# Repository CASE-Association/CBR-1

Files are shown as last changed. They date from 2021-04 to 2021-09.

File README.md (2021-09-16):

# CBR-1
Case Balancing Robot 1

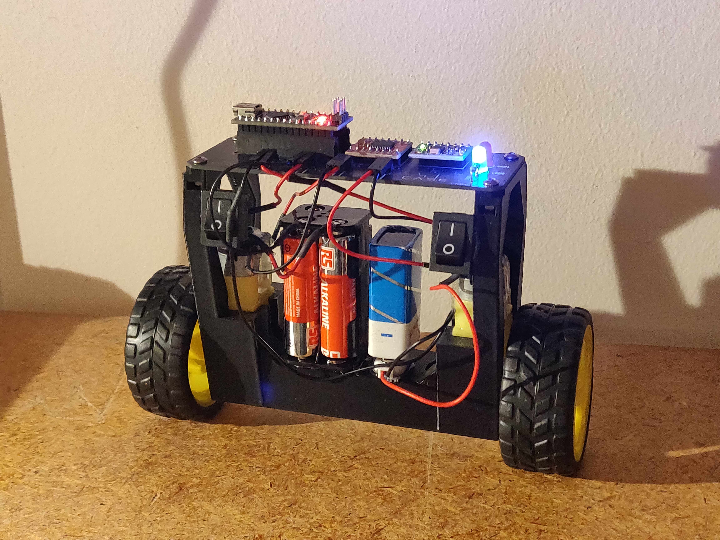
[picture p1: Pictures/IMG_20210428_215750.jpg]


Beginner balancing robot developed by CASE Association.

# Bill of materials
  - 1 x Arduino Nano
  - 1 x TB6612FNG (DC motor driver)
  - 1 x MPU6050 (Inertial measurement unit)
  - 1 x CBR-1 3D-printed chassi
  - 2 x 6V DC motors (with wheels)
  - 1 x Rockerswitch or other switch (between 9V battery and PCB)
  - 1 x 4xAA batteryholder
  - 1 x 9V batteryholder
  - 4 x M3x10 screw (M3x12 might also work)
  - 4 x M3 nut
  - Wires
  - Heatshrink
  - 4 x AA batteries (there are some in the lab you can try out with your bot with but it's a good idea to bring your own batteries)
  - 1 x 9V battery (same with AA batteries, it's nice to bring your own)

Optional:

  - 1 x Rockerswitch or other switch (now between the 4xAA batteryholder and PCB)
  - 2 x LED
  - 2 x Resistors R1 and R2
  - Various pin-connectors
For R1 and R2, use whatever resistance you prefer for LEDs in these applications, but around 300 ohm works fine. We used 100 Ohm for a red LED and 300 Ohm for a blue LED.

All of the components are available to purchase in the iZettle, but feel free to use your own components if you for instance want a more powerful battery to power the motors. The most important thing is that you are able to supply 9-12 V to the Arduino and at least 6 V to the motors (a somewhat higher voltage will work, you'll get more power!). Using 4xAA (4 in series) is the absolute minimum battery solution, considering the max current you get from them.

The 3D-printed chassi can, if not bought through iZettle, be redesigned and 3D-printed if you like. The STL file is provided in the CAD folder, and you can also design things to add to the robot! The picture below shows an example of a way to increase the distance between the ground and the centrum of mass by placing the batteries on top. This makes it easier for the robot to balance!

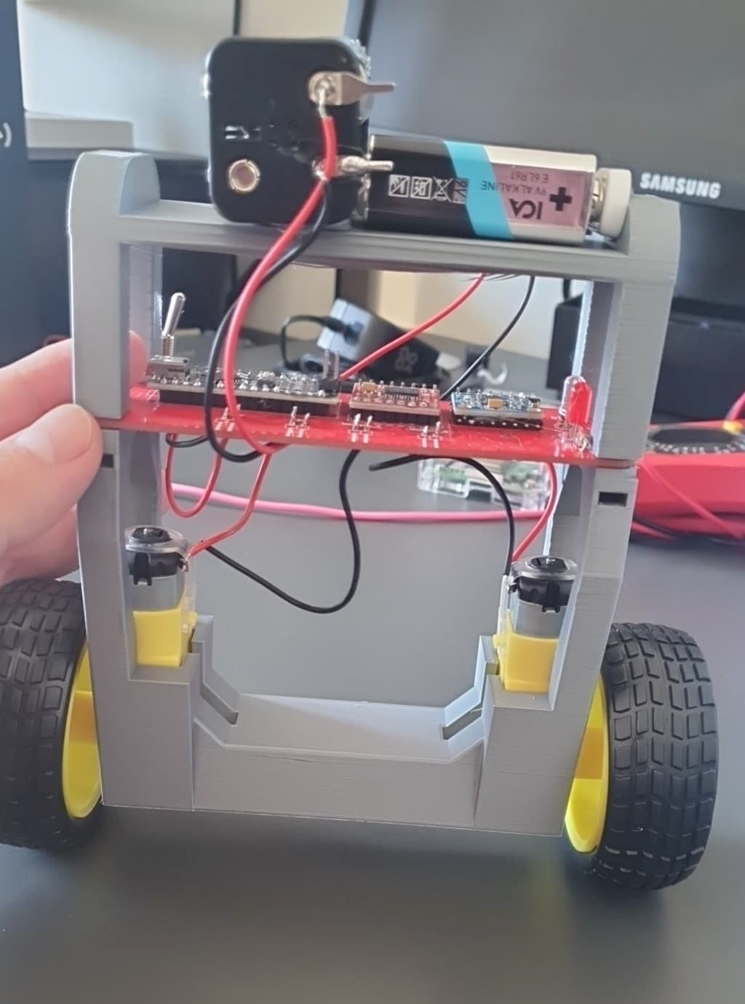
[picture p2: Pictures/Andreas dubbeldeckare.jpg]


The STL file for this extra piece can also be found in the CAD folder.

# Soldering
There's quite a bit of it.

## Soldering components to the PCB

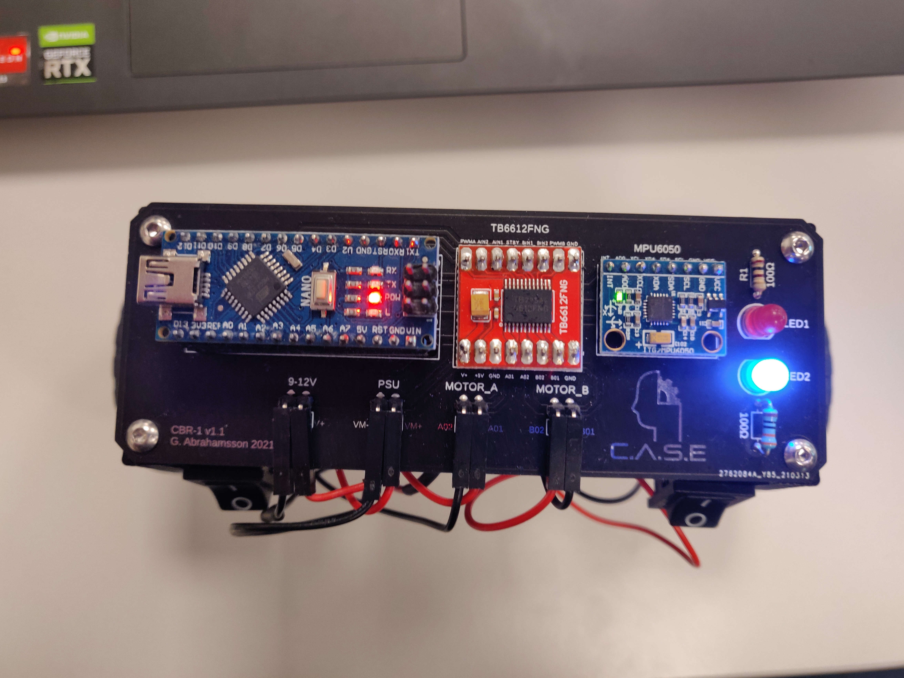
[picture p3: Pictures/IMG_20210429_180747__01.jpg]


The three main components to solder to the PCB are:

  - Arduino Nano
  - TB6612FNG
  - MPU6050

The PCB is marked where to attach each component, but you can solder in two ways:

### Directly to the PCB
This gives the most clean look, but can be quite troublesome if something goes wrong. It's very important that you orient the components in the correct way (they fit both ways, but only one works)! Double check that the ports on the components match the ones on the PCB before soldering.

### With female pin connectors to the PCB
Solder female pin connectors to the PCB and then attach your components to them. This way you can reuse components if you don't feel like buying the same component for another project in the future. If a component fails, you can also replace them much easier.

## LEDs
If you want LEDs on your robot, solder them to the PCB with their respective resistor. Don't forget that LEDs are Light Emitting *Diodes*.The kathode (the shorter pin) must be put into the hole near the "flat side" of the footprint on the PCB. The anode (the longer pin) must be put into the hole near the "round side".

## Wiring

Don't forget heatshrink before you solder!

Connectors can be soldered to the ports for 6-12 V, powersupply (marked "PSU" or "6V"), motor A and motor B if you like. This makes it easier to detach parts of the robot without needing to desolder anything. In the example on page 1, 90° male pin connectors are used on the PCB while the motors and batteries all have female pin connectors soldered to their respective cables.

### Batterypacks
If you only want to use one switch, use it with the 9V battery. This ensures that the only switch used is turning the Arduino Nano on/off (since the 9-12V port is powering the Nano and PSU/6V is powering the motors).
The switch can be between the battery and the positive or the negative pin on the PSU/6V ports, since it's breaking the circuit. We soldered the already attached red wire from the 9V battery to one pin on the switch, and then another wire (dupont-cable with one end cut off) on the other pin on the switch. Another dupont cable was soldered to the other wire from the battery holder to make sure it has a female connector.

The same was done with the 4xAA battery holder, but the wires were soldered to the pins since this particular battery holder does not come with wires already attached.

Repeat this for the other pack, but ignore the switch if you do not want to use two of them. Remember, having control over both batterypacks while the robot is in action is very helpful. We recommend two switches!

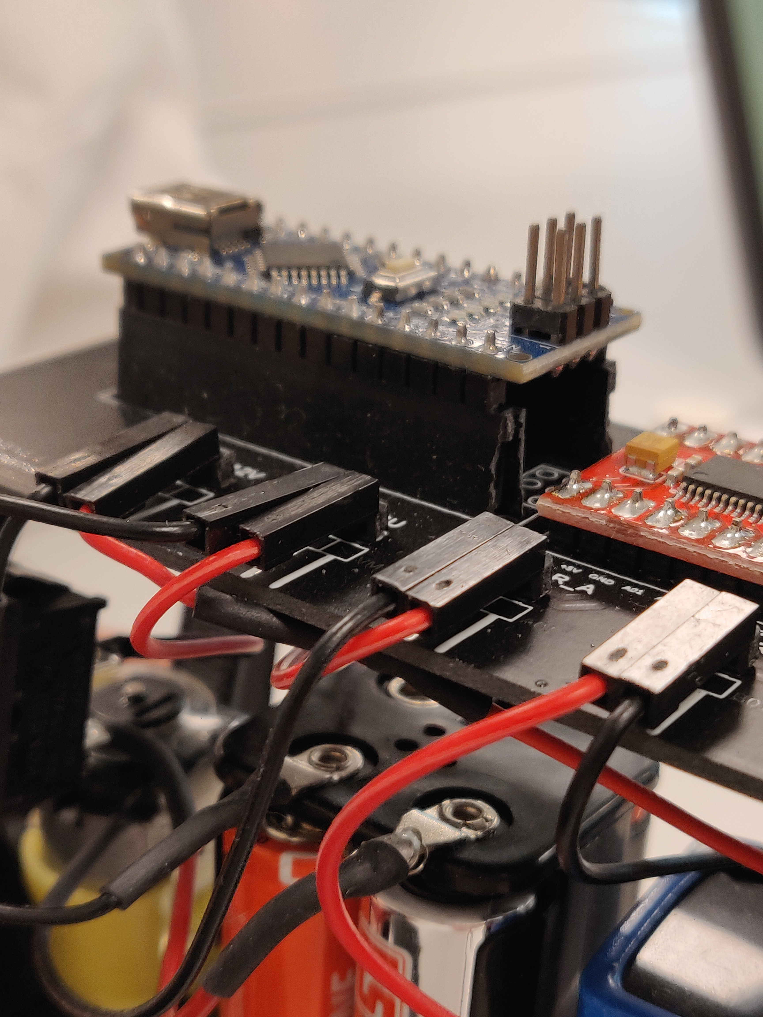
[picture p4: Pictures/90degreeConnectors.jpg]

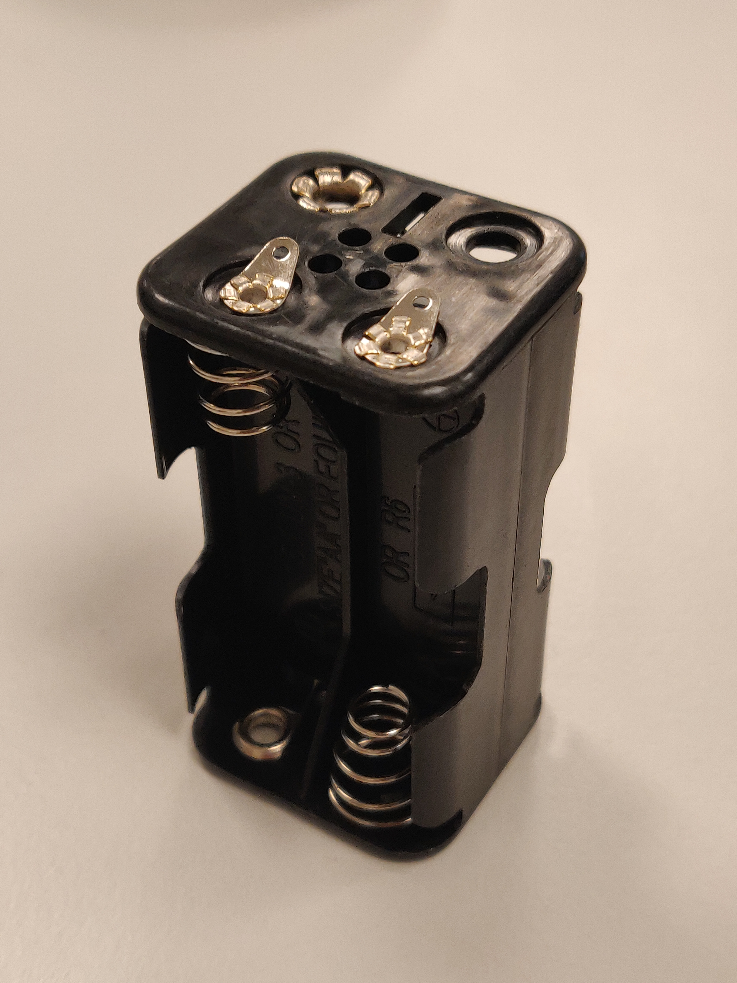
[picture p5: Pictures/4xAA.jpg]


When soldering wires to the batterypacks, don't forget to use red for positive and black for negative! Things get very problematic if they are mixed up!

### Motors
For each motor, solder wires to each of the connections on the motor. Heatshrink is good to use here (don't for get to put it on before you solder!), and applying some hot glue around the connection after everything is done will decrease the risk of the copper breaking from bending. Also, using dupont cables with female pin connectors is a fast way to get wires without having to attach connectors to the end of the wires. Just cut one end off and keep the other!

If the wheels aren't already attached, attach them now.

# Assembly
Bring out the glue gun! 

## Gluing

Everything except for the PCB is attached with hot glue, so just glue on the motors and batterypacks! Remember not to orient the packs in a way where you can't remove/attach batteries.

## PCB
Drop in an M3 nut in each hole and screw on the PCB with the M3 screws. It's possible to glue the PCB to the chassi but it's made to be assembled with nuts and screws. 

## Connecting the wires
If you're not using connectors, replace "connect" with "solder":
  - Connect the wires from the 9V battery holder to the 9-12V port.
  - Connect the wires from the 4xAA battery holder to the PSU/6V port.
  - Connect the wires from one of the motor to the "Motor A" port. It does not matter which wire goes to which pin, this can be corrected in the code if the motor turns the wrong way.
  - Connect the wires from the other motor to the "Motor B" port.

The robot is now fully assembled!

# Software

PlatformIO was used for this project. The code can be found in the "Code" folder.

## Libraries
The following libraries are needed:
  - PID_v1.h
  - I2Cdev.h
  - MPU6050_6Axis_MotionApps20.h

Make sure they are in your project!

## Using the code

Upload the code to the Nano. Do not freak out if it doesn't work at first! There's a few things that might need to be adjusted.

### Motor rotation directions
When tilting the robot to one direction, the motors should turn in a way that drives it in that direction. If a specific motor does not turn that direction, you can switch the connectors.
This will switch the direction the motor turns. Do this to both motors so that they drive in the direction the robot tilts.

If you do not have connectors, but have soldered the wires to each port, you can switch the direction of the motors in the code.
This is done by changing the LOW to HIGH or HIGH to LOW of both ports on a specific motor in the functions *Forward* and *Reverse*.
Having in1A LOW and in2A HIGH will rotate the motor in one direction, and switching in1A to HIGH and in2A to LOW will make it rotate
the other direction.

top

You can achieve the same effect by switching the output from negative to positive or vice versa:

top

### Calibration
The robot might not perform optimally with the default values included. This will be fixed here.

#### Target angle
If the robot is trying to escape everytime you set it down, you might have to calibrate the setpoint.
If it's too low or too high, the robot will correct itself to a too low of an angle, making it tilt and therefore accelerating
in that direction.

top

Problems with the setpoint can also occur if the MPU6050 is not soldered/connected parallell to the PCB.
If you feel comfortable trying to bend it parallell, go ahead, but adjusting the setpoint in the code also works.

#### PID
If the robot isn't balancing, or trying too violently, you can adjust the PID values (especially if you've attached the batteries
in another way compared to ours at the top of this page!).

Start by adjusting the *Kp* value. This affects the output based on the difference from the measured and target value.
If it's too slow or "weak", increase the value. If it's too violent and jerky, decrease the value.

After that, move on to *Kd*. This affects the output based on the derivative.
If it's too jittery, reduce the value.

Lastly, adjust *Ki*. This affects the output based on the integral.
Start from a low value and increase it until it works.

It should now balance on its own!

#### LEDs
You can control the LEDs (if you have them) by writing a 1 or a 0 to their respective ports:

top

In the provided code, the LEDs will show which direction the robot is currently travelling in.

# Improvements

There's a lot about this robot that can be improved. Here's a list of things to improve if you'd like:
  - 3D-printed chassi: Design your own chassi or some piece to be attached to it! The center of mass needs to get higher!
  - Code that takes velocity into concideration: Currently, the robot is satisfied as long as it's standing upright, even if its travelling at max speed. Try to fix this in the code!
  - Improved PCB: If you're into SMD, you can design a PCB with no throughhole components and only surface mounted ones. It will look much cooler!
  - Wireless controls: You could attach for instance an NRF24L01 to enable wireless communication with a controller!
  - Other batteries: It is possible to use for instance LiPo batteries to enable more power, while also only needing one battery.
  - Measure the angle that the motors rotate to: Since regular DC motors and no stepper motors (or something similar) are used in this project, the robot does not know how much the wheels have actually rotated. It is possible to use sensors to measure this and to use the information in conjunction with the controls-code.

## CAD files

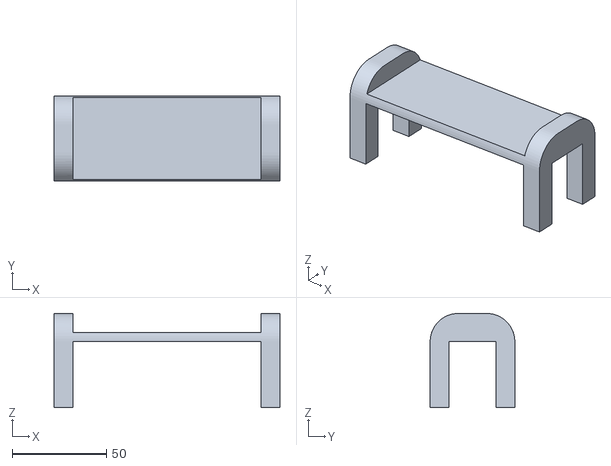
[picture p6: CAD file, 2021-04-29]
CAD/Brygga-Balans-v1.stl
120.0 x 45.0 x 50.0

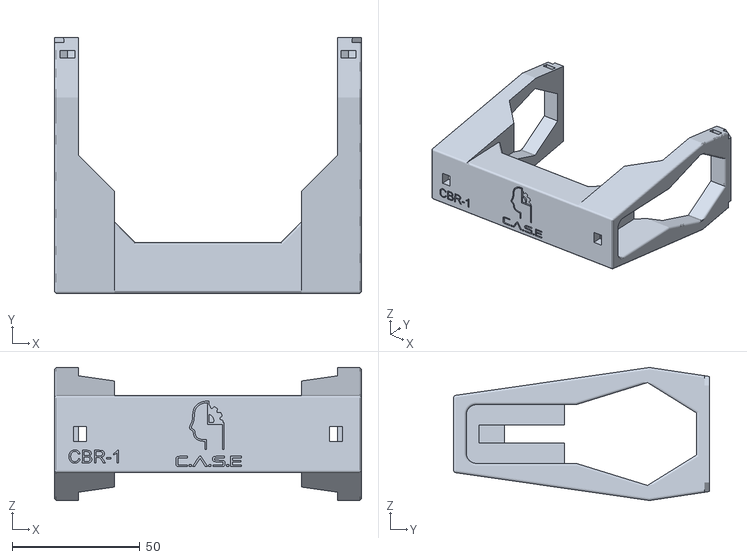
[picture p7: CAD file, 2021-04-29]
CAD/CBR-1 Chassi 2.2.stl
120.0 x 100.0 x 52.0

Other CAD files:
PCB/CBR-1_PCB_Design v36.f3z

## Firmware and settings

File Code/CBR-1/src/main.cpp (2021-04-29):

#include <Arduino.h>
#include <PID_v1.h>
#include <I2Cdev.h>
#include <MPU6050_6Axis_MotionApps20.h>
 
int pwmA = 5;
int in1A = 3;
int in2A = 4;
 
int pwmB = 6;
int in1B = 7;
int in2B = 8;

int LED2 = 11;
int LED1 = 12;
 
int n1 = 0;
int n2 = 0;

MPU6050 mpu;

// MPU control/status vars
bool dmpReady = false;  // set true if DMP init was successful
uint8_t mpuIntStatus;   // holds actual interrupt status byte from MPU
uint8_t devStatus;      // return status after each device operation (0 = success, !0 = error)
uint16_t packetSize;    // expected DMP packet size (default is 42 bytes)
uint16_t fifoCount;     // count of all bytes currently in FIFO
uint8_t fifoBuffer[64]; // FIFO storage buffer

// orientation/motion vars
Quaternion q;           // [w, x, y, z]         quaternion container
VectorFloat gravity;    // [x, y, z]            gravity vector
float ypr[3];           // [yaw, pitch, roll]   yaw/pitch/roll container and gravity vector

/*********Tune these 4 values for your BOT*********/

double setpoint = 180; //set the value when the bot is perpendicular to ground using serial monitor. 

//#############################################
//Change those Values according to your Design
//#############################################
double Kp = 15;  // Set this first
double Ki = 200; // Finally set this 
double Kd = 0.6; // Set this second
//#############################################

double input, output;
PID pid(&input, &output, &setpoint, Kp, Ki, Kd, DIRECT);

volatile bool mpuInterrupt = false;     // indicates whether MPU interrupt pin has gone high

void dmpDataReady()
{
    mpuInterrupt = true;
}


void Forward() //Code to rotate the wheel forward 
{
    digitalWrite(LED1,0);
    digitalWrite(LED2,1);
    
    digitalWrite(in1A, HIGH);
    digitalWrite(in2A, LOW);
 
    digitalWrite(in1B, HIGH);
    digitalWrite(in2B, LOW);

    analogWrite(pwmA, output);
    analogWrite(pwmB, output);

    Serial.print("F"); //Debugging information 
}

void Reverse() //Code to rotate the wheel Backward  
{
    digitalWrite(LED1,1);
    digitalWrite(LED2,0);

    digitalWrite(in1A, LOW);
    digitalWrite(in2A, HIGH);
 
    digitalWrite(in1B, LOW);
    digitalWrite(in2B, HIGH);

    analogWrite(pwmA, -1*output);
    analogWrite(pwmB, -1*output);

    Serial.print("R");
}

void Stop() //Code to stop both the wheels
{
    digitalWrite(LED1,0);
    digitalWrite(LED2,0);

    digitalWrite(in1A, LOW);
    digitalWrite(in2A, LOW);
 
    digitalWrite(in1B, LOW);
    digitalWrite(in2B, LOW);

    analogWrite(pwmA, 0);
    analogWrite(pwmB, 0);

    Serial.print("S");
}

void setup(){

  pinMode(pwmA, OUTPUT);
  pinMode(pwmB, OUTPUT);
  pinMode(in1A, OUTPUT);
  pinMode(in2A, OUTPUT);
  pinMode(in1B, OUTPUT);
  pinMode(in2B, OUTPUT);

  pinMode(LED1,OUTPUT);
  pinMode(LED2,OUTPUT);


  //Serial.begin(9600);
  
  // initialize device
    Serial.println(F("Initializing I2C devices..."));
    mpu.initialize();

     // verify connection
    Serial.println(F("Testing device connections..."));
    Serial.println(mpu.testConnection() ? F("MPU6050 connection successful") : F("MPU6050 connection failed"));

    // load and configure the DMP
    devStatus = mpu.dmpInitialize();

    
    // supply your own gyro offsets here, scaled for min sensitivity
    mpu.setXGyroOffset(220);
    mpu.setYGyroOffset(76);
    mpu.setZGyroOffset(-85);
    mpu.setZAccelOffset(1688); 

      // make sure it worked (returns 0 if so)
    if (devStatus == 0)
    {
        // turn on the DMP, now that it's ready
        Serial.println(F("Enabling DMP..."));
        mpu.setDMPEnabled(true);

        // enable Arduino interrupt detection
        Serial.println(F("Enabling interrupt detection (Arduino external interrupt 0)..."));
        attachInterrupt(0, dmpDataReady, RISING);
        mpuIntStatus = mpu.getIntStatus();

        // set our DMP Ready flag so the main loop() function knows it's okay to use it
        Serial.println(F("DMP ready! Waiting for first interrupt..."));
        dmpReady = true;

        // get expected DMP packet size for later comparison
        packetSize = mpu.dmpGetFIFOPacketSize();
        
        //setup PID
        pid.SetMode(AUTOMATIC);
        pid.SetSampleTime(10);
        pid.SetOutputLimits(-255, 255);  
    }
    else
    {
        // ERROR!
        // 1 = initial memory load failed
        // 2 = DMP configuration updates failed
        // (if it's going to break, usually the code will be 1)
        Serial.print(F("DMP Initialization failed (code "));
        Serial.print(devStatus);
        Serial.println(F(")"));
    }

}

void loop() {

  /*
  motorSpeed1 = map(analogRead(ASDASD), 0, 1023, 0, 255);
  motorSpeed2 = map(analogRead(50ASDASD0), 0, 1023, 0, 255);  
    */

// if programming failed, don't try to do anything
    if (!dmpReady) return;

    // wait for MPU interrupt or extra packet(s) available
    while (!mpuInterrupt && fifoCount < packetSize)
    {
        //no mpu data - performing PID calculations and output to motors     
        pid.Compute();   
        
        //Print the value of Input and Output on serial monitor to check how it is working.
        Serial.print(input); Serial.print(" =>"); Serial.println(output);
               
        if (input>150 && input<200){//If the Bot is falling 
          
        if (output>0) //Falling towards front 
        Forward(); //Rotate the wheels forward 
        else if (output<0) //Falling towards back
        Reverse(); //Rotate the wheels backward 
        }
        else //If Bot not falling
        Stop(); //Hold the wheels still
        
    }

    // reset interrupt flag and get INT_STATUS byte
    mpuInterrupt = false;
    mpuIntStatus = mpu.getIntStatus();

    // get current FIFO count
    fifoCount = mpu.getFIFOCount();

    // check for overflow (this should never happen unless our code is too inefficient)
    if ((mpuIntStatus & 0x10) || fifoCount == 1024)
    {
        // reset so we can continue cleanly
        mpu.resetFIFO();
        Serial.println(F("FIFO overflow!"));

    // otherwise, check for DMP data ready interrupt (this should happen frequently)
    }
    else if (mpuIntStatus & 0x02)
    {
        // wait for correct available data length, should be a VERY short wait
        while (fifoCount < packetSize) fifoCount = mpu.getFIFOCount();

        // read a packet from FIFO
        mpu.getFIFOBytes(fifoBuffer, packetSize);
        
        // track FIFO count here in case there is > 1 packet available
        // (this lets us immediately read more without waiting for an interrupt)
        fifoCount -= packetSize;

        mpu.dmpGetQuaternion(&q, fifoBuffer); //get value for q
        mpu.dmpGetGravity(&gravity, &q); //get value for gravity
        mpu.dmpGetYawPitchRoll(ypr, &q, &gravity); //get value for ypr

        input = ypr[1] * 180/M_PI + 180;

   }
  
}
